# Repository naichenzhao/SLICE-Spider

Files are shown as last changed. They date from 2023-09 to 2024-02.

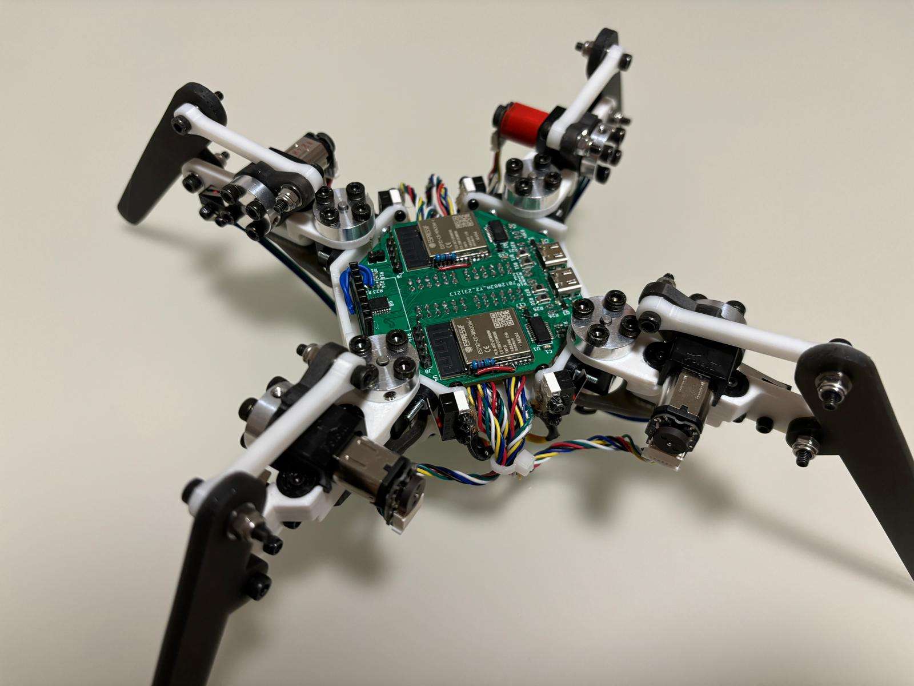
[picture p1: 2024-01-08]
images/IMG-20240107-WA0005.jpg

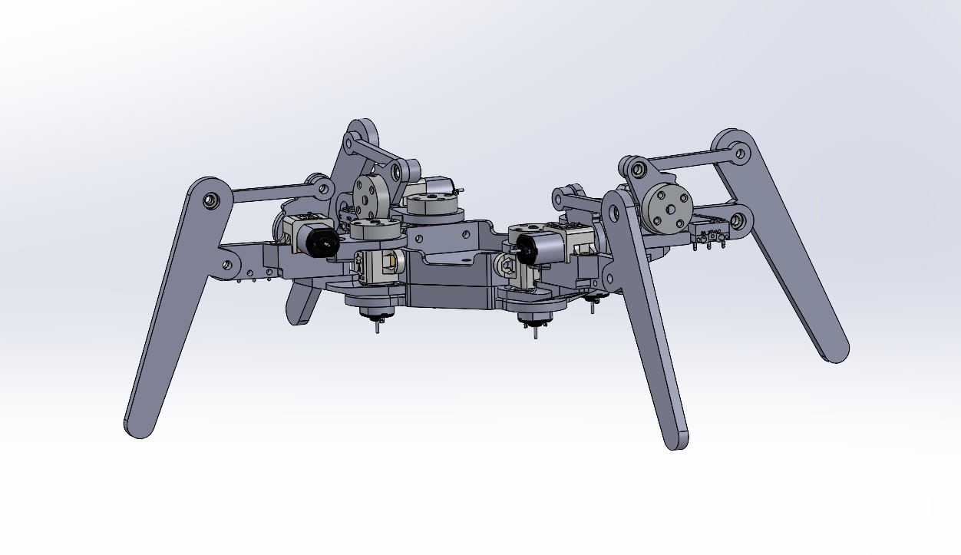
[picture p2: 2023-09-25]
images/Screenshot 2023-09-24 220727.jpg

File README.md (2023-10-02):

# Spider Bot for SLICE

something something, torque controlled robot spider



## Manufacturing
- SLS_Leg_Lower and SLS_Lever_Lower can be laser cut out of acrylic
- Everything else should be 3D printed

## BOM

Parts needed per spider
- 8x 12V DC Motor: https://www.pololu.com/product/3046
- 8x Enoder for motor: https://www.pololu.com/product/4761
- 8x M3 Motor hub w/ M3 screws: https://www.pololu.com/product/1996
- 8x Homing switches for the legs: https://www.amazon.com/Cylewet-25Pcs-Switch-Arduino-CYT1073/dp/B073TYWX86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
- 12x M3 flanged bearing for joints: https://www.amazon.com/uxcell-Flanged-3x6x2-5mm-Shielded-Bearings/dp/B08H27NJ5N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
- 16x M2 threaded heat insert: https://www.mcmaster.com/94180A307/

- Assortment of M2 and M3 screws/nuts

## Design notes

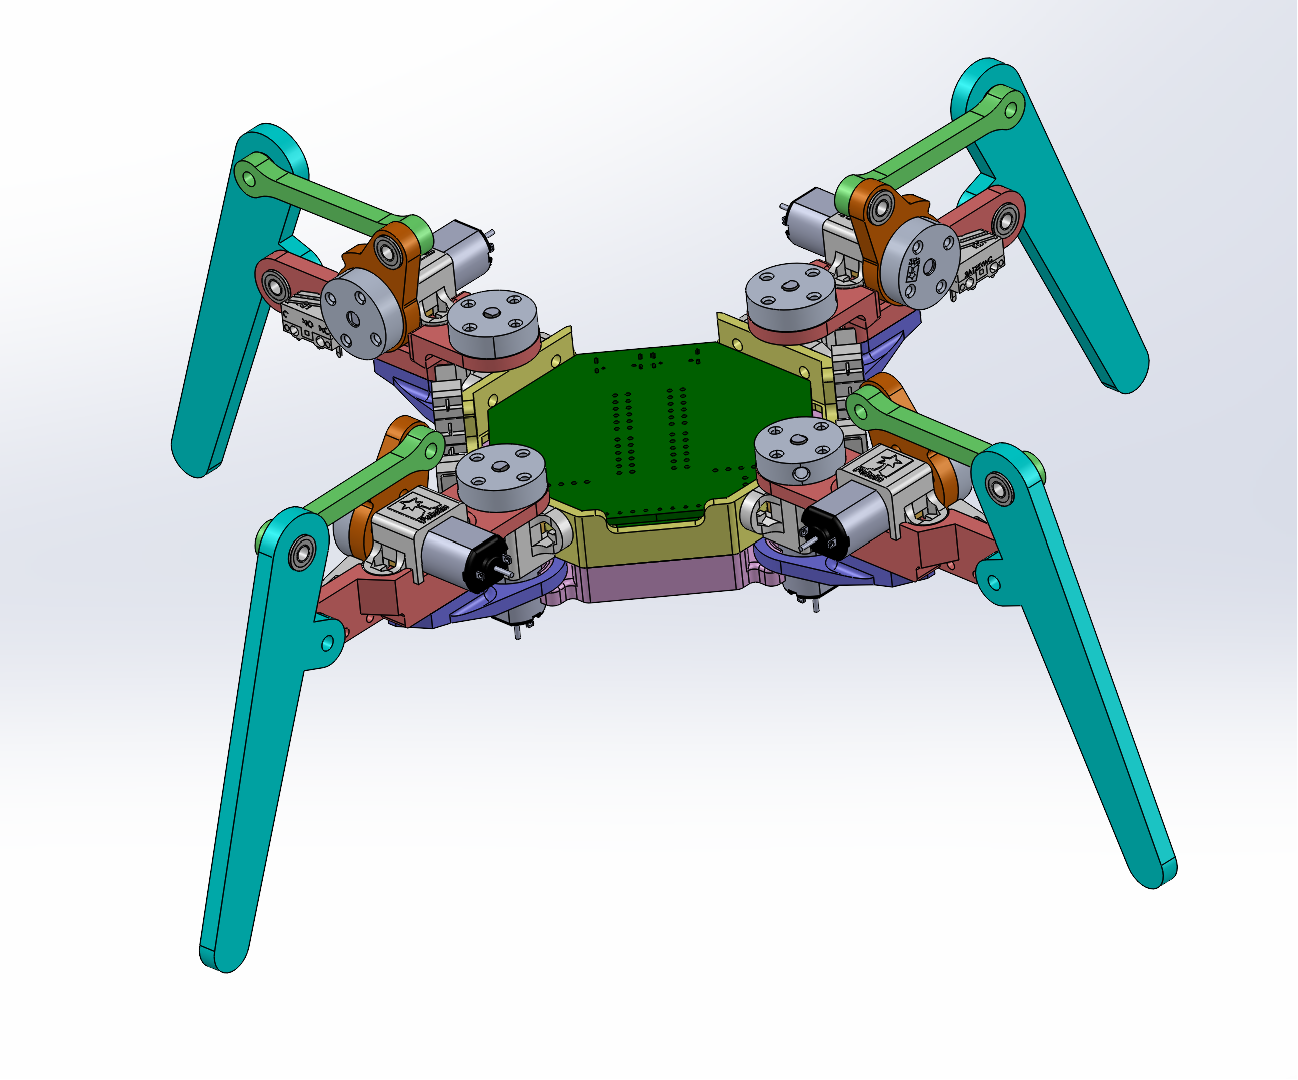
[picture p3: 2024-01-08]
images/Screenshot 2024-01-07 225647.png

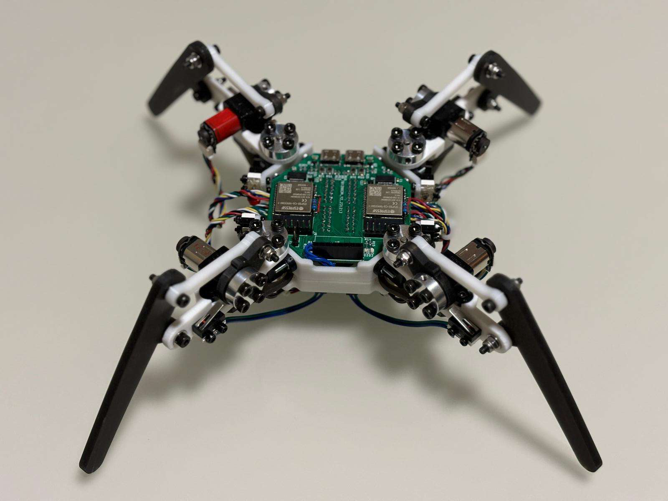
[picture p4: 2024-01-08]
images/IMG-20240107-WA0008.jpg

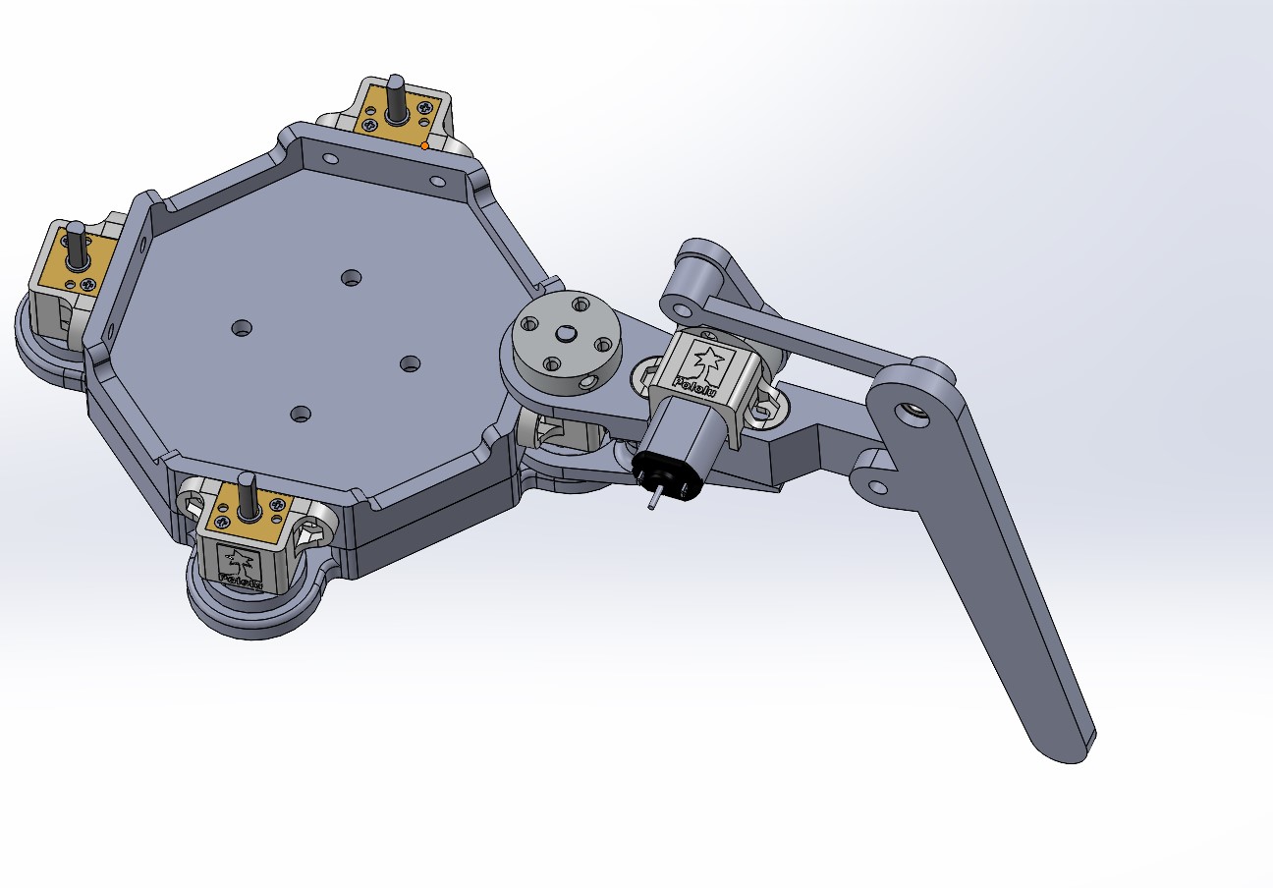
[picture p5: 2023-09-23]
images/Screenshot 2023-09-23 005408.jpg

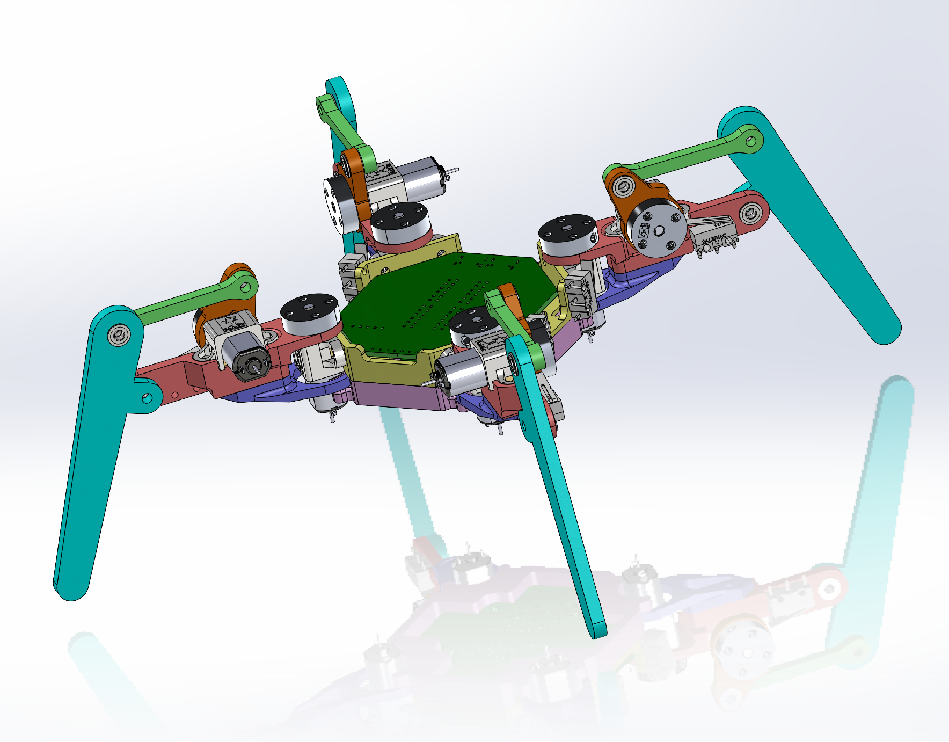
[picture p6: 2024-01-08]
images/Screenshot 2024-01-07 225526.png

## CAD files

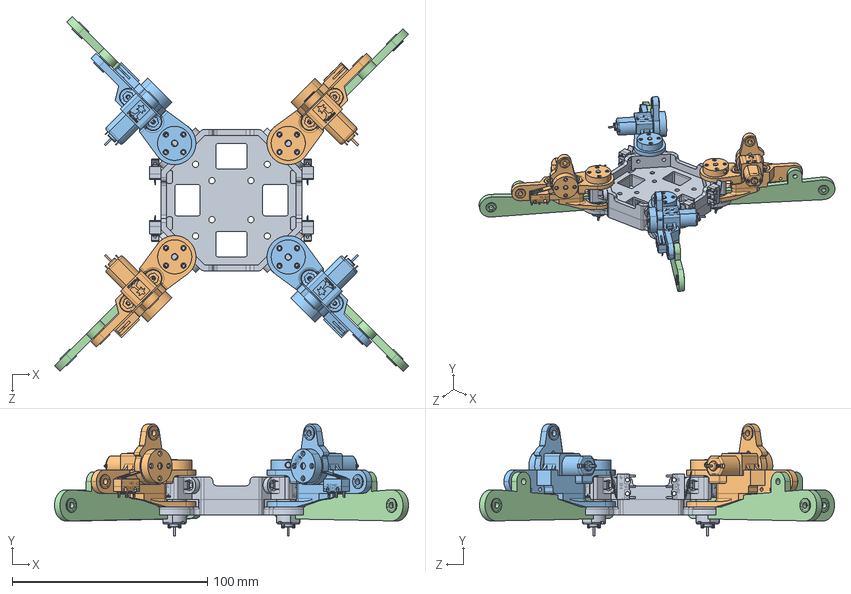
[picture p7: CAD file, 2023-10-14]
testing URDF Exporting/spider-viz.SLDASM
181.6 x 57.3 x 182.0 mm
Spider_body
Spider_upperleg_1 x 2
Spider_upperleg_2 x 2
Spider_lowerleg x 4

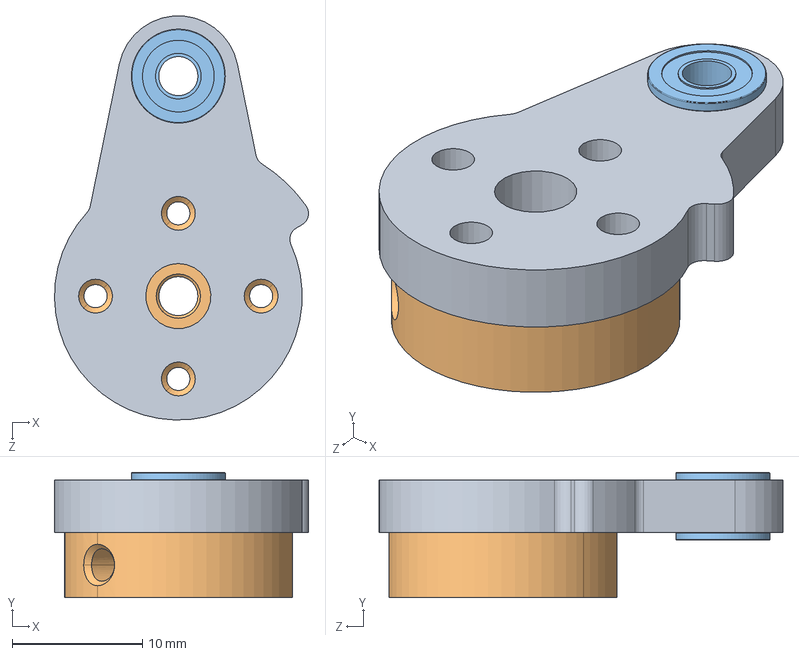
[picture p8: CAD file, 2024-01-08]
Solidoworks_Files/Spider_lever_2.SLDASM
19.5 x 9.60 x 31.0 mm
SLS_Lever_upper
shaft_mount
MF63zz 3x6x2.5mm Flanged Bearing.step x 2

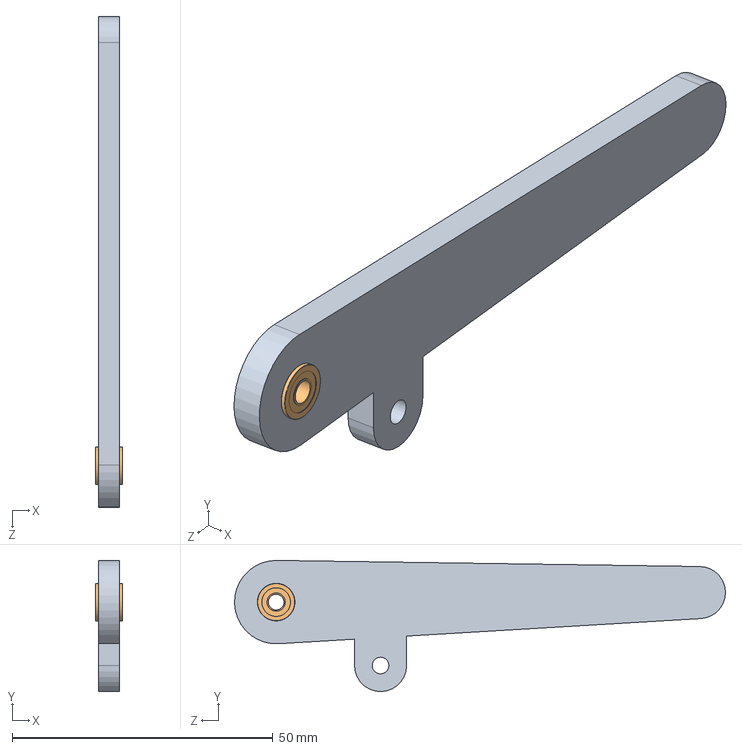
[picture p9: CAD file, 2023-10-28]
Solidoworks_Files/Spider_lowerleg.SLDASM
5.20 x 25.2 x 94.2 mm
SLS_leg_lower
MF63zz 3x6x2.5mm Flanged Bearing.step x 2

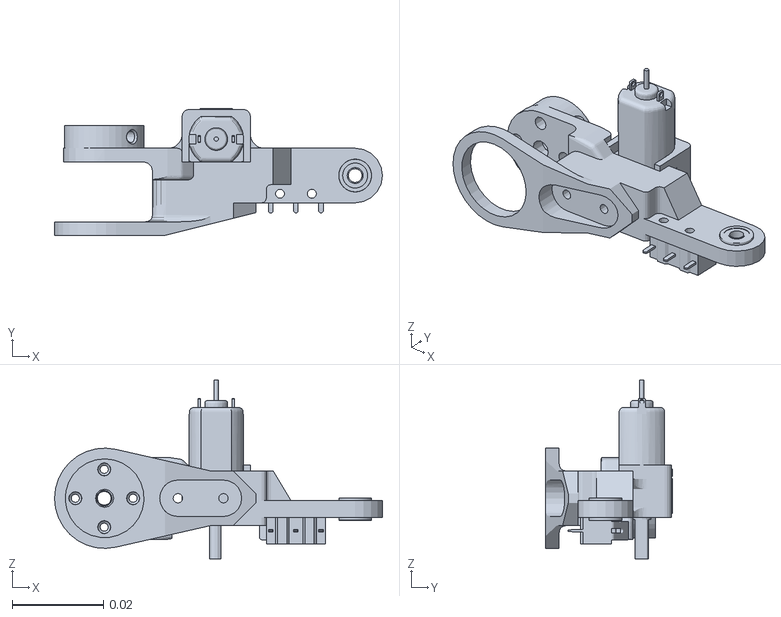
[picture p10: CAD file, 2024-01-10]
catkin_ws/src/spider-viz/meshes/Upper1_Link.STL
0.072 x 0.0279 x 0.0393

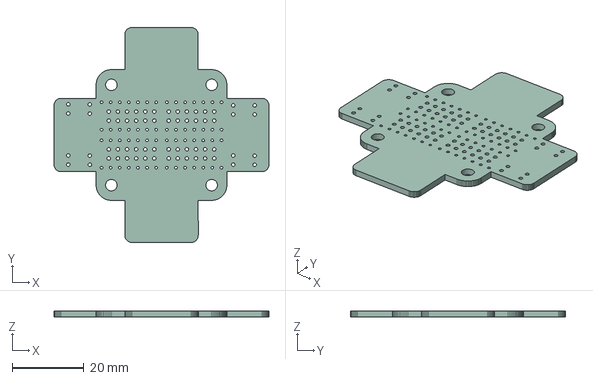
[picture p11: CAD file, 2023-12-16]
PCB/V1/Spider_Lower/Spider_Lower.step
60.0 x 60.0 x 1.58 mm

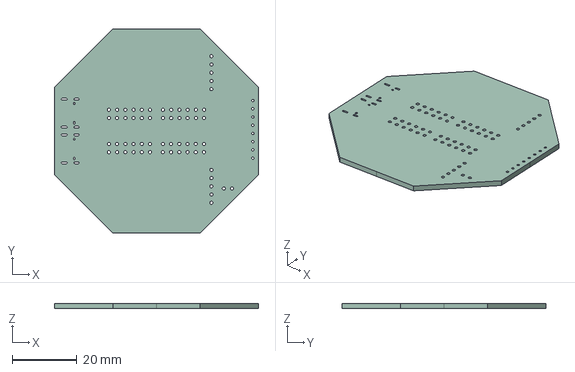
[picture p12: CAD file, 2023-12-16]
PCB/V1/Spider_Upper/Spider_Upper.step
63.0 x 63.0 x 1.58 mm

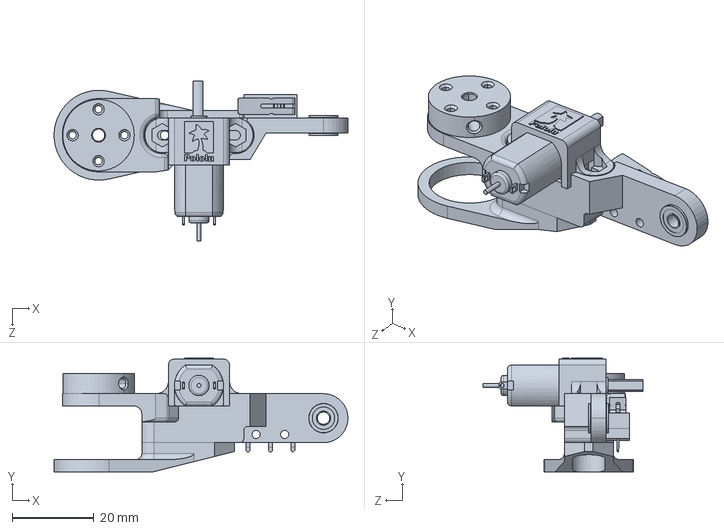
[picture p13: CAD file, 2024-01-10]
Solidoworks_Files/asm_parts/Spider_upperleg_1.SLDPRT
72.0 x 27.9 x 39.3 mm

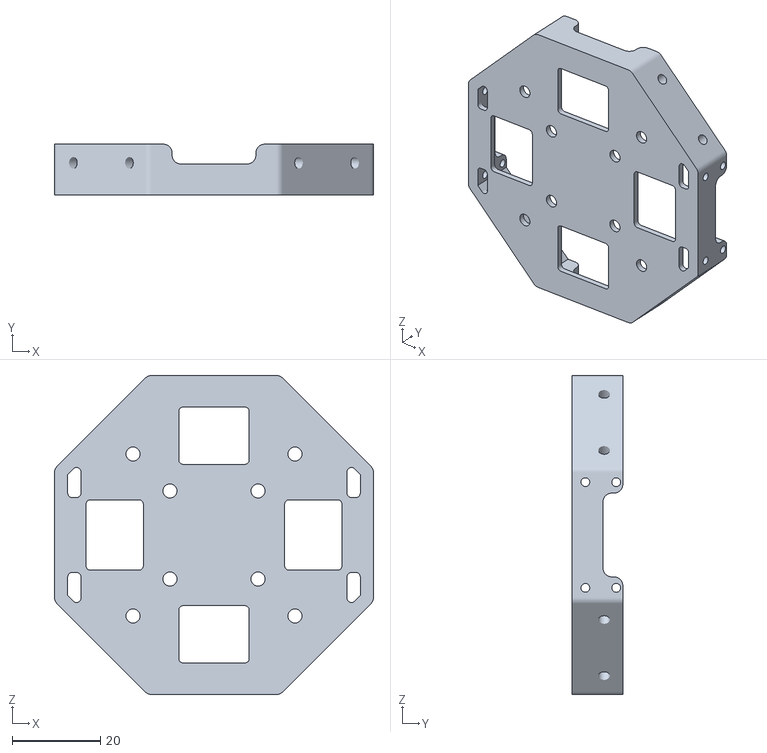
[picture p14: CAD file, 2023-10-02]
STL_Files/SLS_body.STL
72.4 x 11.5 x 72.4

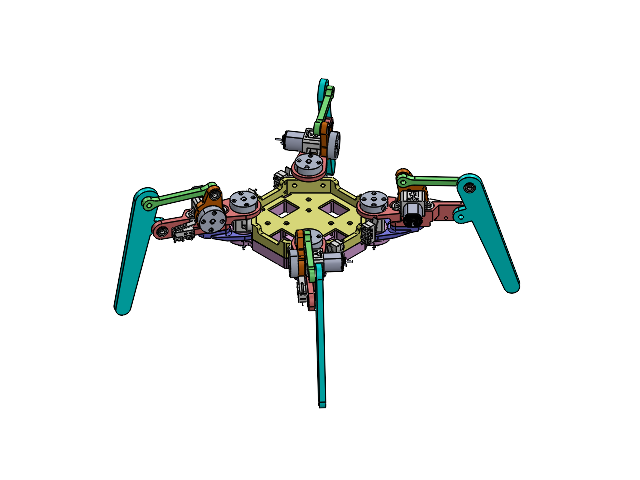
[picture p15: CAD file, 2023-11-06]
onshape_export/onshape_export.SLDASM
Spider_body
Spider_upperleg_1 x 2
Spider_upperleg_2 x 2
Spider_lowerleg x 4
SLS_lever_lower x 4
Spider_lever_2 x 2
Spider_lever x 2

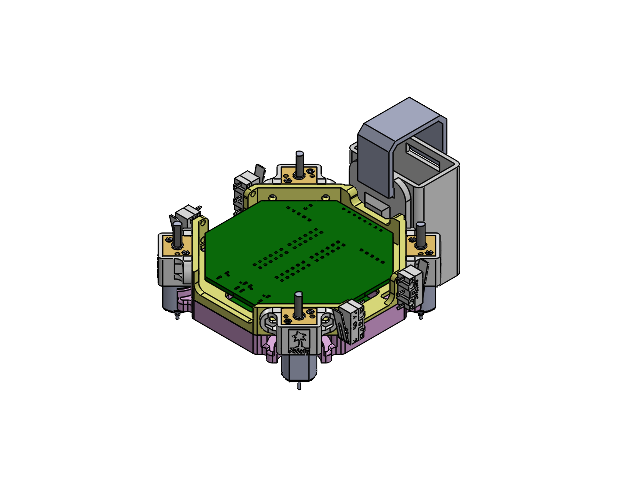
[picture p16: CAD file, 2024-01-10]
Solidoworks_Files/Spider_body.SLDASM
SLS_body
12V_Motor x 4
Limit_Switch x 4
SLS_lower_body
PCB_Lower
PCB_Upper
6mm_magnet x 4
batery_case
battery_case_clip

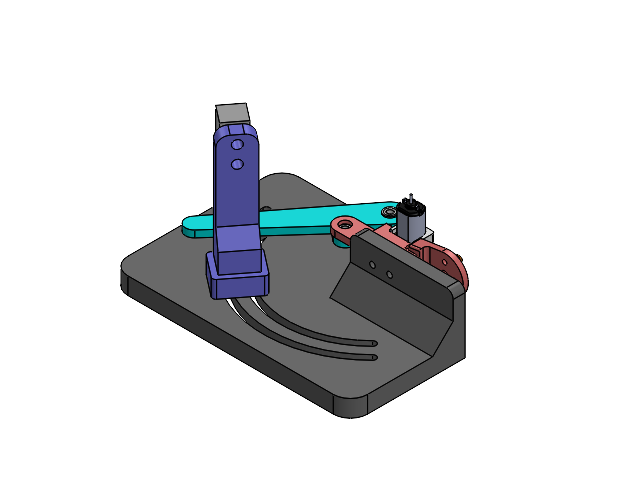
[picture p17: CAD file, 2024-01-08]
Testbenches/leg_TB_asm.SLDASM
leg_TB_frame
SLS_leg_upper_M
12V_Motor
MF63zz 3x6x2.5mm Flanged Bearing.step x 5
SLS_Lever_upper
shaft_mount
SLS_leg_lower
SLS_lever_lower
Strain_Gauge
Let_TB_slider

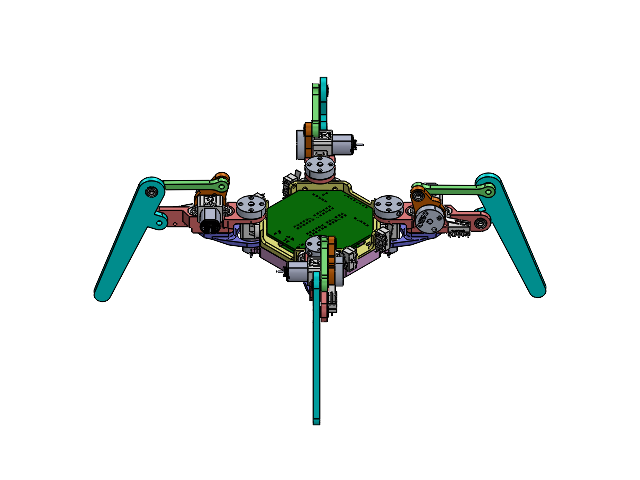
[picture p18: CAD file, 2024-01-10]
Solidoworks_Files/TLA_Spider.SLDASM
SLS_body
12V_Motor x 8
Limit_Switch x 8
SLS_lower_body
PCB_Lower
PCB_Upper
6mm_magnet x 4
batery_case
battery_case_clip
SLS_leg_upper x 2
MF63zz 3x6x2.5mm Flanged Bearing.step x 24
SLS_leg_upper_base x 4
shaft_mount x 8
SLS_leg_upper_M x 2
SLS_leg_lower x 4
SLS_lever_lower x 4
SLS_Lever_upper x 4

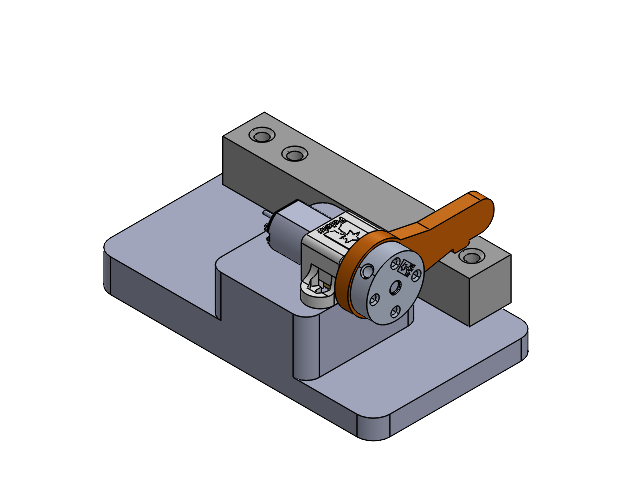
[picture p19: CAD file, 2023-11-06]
Testbenches/motor_TB_asm.SLDASM
motor_TB_frame
Strain_Gauge
12V_Motor
motor_TB_lever
shaft_mount

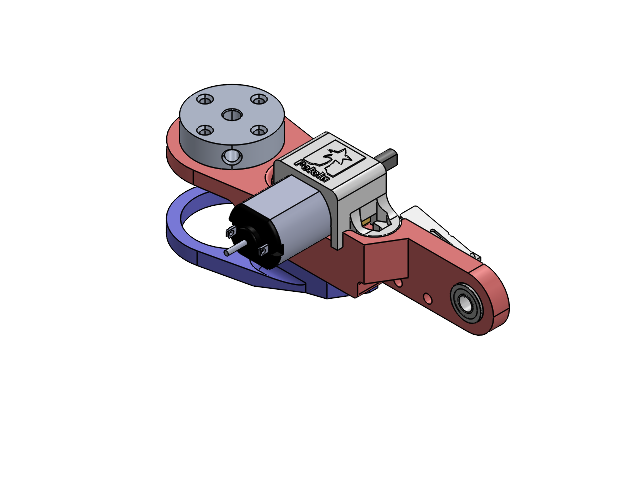
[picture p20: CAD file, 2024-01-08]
Solidoworks_Files/Spider_upperleg_1.SLDASM
SLS_leg_upper
Limit_Switch
12V_Motor
MF63zz 3x6x2.5mm Flanged Bearing.step x 2
SLS_leg_upper_base
shaft_mount

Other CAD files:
Solidoworks_Files/Spider_upperleg_2.SLDASM
Solidoworks_Files/Spider_lever.SLDASM
catkin_ws/src/spider-viz/meshes/Upper2_Link.STL
onshape_export/Spider_lever.SLDPRT
Archive/onshape_export/Spider_lever.SLDPRT
Archive/onshape_export/Spider_lever_2.SLDPRT
Archive/onshape_export/Spider_lowerleg.SLDPRT
Archive/onshape_export/Spider_upperleg_1.SLDPRT
Archive/onshape_export/Spider_upperleg_2.SLDPRT
Archive/testing URDF Exporting/Spider_lowerleg.SLDPRT
Archive/testing URDF Exporting/Spider_upperleg_1.SLDPRT
Archive/testing URDF Exporting/Spider_upperleg_2.SLDPRT
STL_Files/SLS_Lever_upper.STL
STL_Files/SLS_leg_lower.STL
STL_Files/SLS_leg_upper.STL
STL_Files/SLS_leg_upper_M.STL
STL_Files/SLS_leg_upper_base.STL
STL_Files/SLS_lever_lower.STL
STL_Files/SLS_lower_body.STL
Solidoworks_Files/12V_Motor.SLDPRT
Solidoworks_Files/6mm_magnet.SLDPRT
Solidoworks_Files/Limit_Switch.SLDPRT
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

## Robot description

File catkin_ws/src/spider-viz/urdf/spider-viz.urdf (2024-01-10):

<?xml version="1.0" encoding="utf-8"?>
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
<robot name="spider-viz">
  <link name="base_link">
    <inertial>
      <origin xyz="0.0266900629514275 0.0373682215528626 0.0414401671660664" rpy="0 0 0" />
      <mass value="0.0599747186219502" />
      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
    </inertial>
    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
  </link>
  <link name="Upper0_Link">
    <inertial>
      <origin xyz="0.021476139074384 0.015254727578512 -0.0014907670536348" rpy="0 0 0" />
      <mass value="0.0112993413960727" />
      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
    </inertial>
    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
  </link>
  <joint name="Upper0" type="revolute">
    <origin xyz="-0.00245284745286685 -0.0237725392912402 0.0320074126580795" rpy="1.5707963267949 0 3.14159265358979" />
    <parent link="base_link" />
    <child link="Upper0_Link" />
    <axis xyz="0 1 0" />
    <limit effort="1000.0" lower="-1.57" upper="0.17" velocity="0.5"/>
  </joint>
  <link name="Lower0_Link">
    <inertial>
      <origin xyz="-0.00200000000000073 -0.0121644422551732 0.0152866791815001" rpy="0 0 0" />
      <mass value="0.00511403475106287" />
      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
    </inertial>
    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
  </link>
  <joint name="Lower0" type="revolute">
    <origin xyz="0.0550943670538193 0.01315 -9.9999999999479E-05" rpy="1.57079632679491 -1.5707963267949 0" />
    <parent link="Upper0_Link" />
    <child link="Lower0_Link" />
    <axis xyz="1 0 0" />
    <limit effort="1000.0" lower="-0.96" upper="0.70" velocity="0.5"/>
  </joint>
  <link name="Upper1_Link">
    <inertial>
      <origin xyz="0.0213801728228362 0.0152547283369141 0.0014673545578197" rpy="0 0 0" />
      <mass value="0.0112993383446934" />
      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
    </inertial>
    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
  </link>
  <joint name="Upper1" type="revolute">
    <origin xyz="-0.0024528474528662 -0.0820568105387026 0.0320074126580794" rpy="1.5707963267949 0 3.14159265358979" />
    <parent link="base_link" />
    <child link="Upper1_Link" />
    <axis xyz="0 1 0" />
      <limit effort="1000.0" lower="-0.17" upper="1.85" velocity="0.5"/>
  </joint>
  <link name="Lower1_Link">
    <inertial>
      <origin xyz="0.0020000000000001 -0.012164442255174 0.0152866791815" rpy="0 0 0" />
      <mass value="0.00511403475106288" />
      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
    </inertial>
    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
  </link>
  <joint name="Lower1" type="revolute">
    <origin xyz="0.055 0.0131500000000001 9.99999999997392E-05" rpy="1.57079632679491 -1.5707963267949 0" />
    <parent link="Upper1_Link" />
    <child link="Lower1_Link" />
    <axis xyz="1 0 0" />
    <limit effort="1000.0" lower="-0.96" upper="0.70" velocity="0.5"/>
  </joint>
  <link name="Upper2_Link">
    <inertial>
      <origin xyz="0.0214745398766555 0.0152547283369141 0.00146735455781985" rpy="0 0 0" />
      <mass value="0.0112993383446934" />
      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
    </inertial>
    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
  </link>
  <joint name="Upper2" type="revolute">
    <origin xyz="0.055831423794595 -0.02377253929124 0.0320074126580794" rpy="1.5707963267949 0 0" />
    <parent link="base_link" />
    <child link="Upper2_Link" />
    <axis xyz="0 1 0" />
    <limit effort="1000.0" lower="-0.17" upper="1.57" velocity="0.5"/>
  </joint>
  <link name="Lower2_Link">
    <inertial>
      <origin xyz="0.00200000000000116 -0.0121644422551723 0.0152866791815003" rpy="0 0 0" />
      <mass value="0.00511403475106288" />
      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
    </inertial>
    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
  </link>
  <joint name="Lower2" type="revolute">
    <origin xyz="0.0550943670538194 0.0131500000000001 0.000100000000000329" rpy="1.57079632679489 -1.5707963267949 0" />
    <parent link="Upper2_Link" />
    <child link="Lower2_Link" />
    <axis xyz="1 0 0" />
    <limit effort="1000.0" lower="-0.96" upper="0.70" velocity="0.5"/>
  </joint>
  <link name="Upper3_Link">
    <inertial>
      <origin xyz="0.0214761390743841 0.0152547275785121 -0.00149076705363482" rpy="0 0 0" />
      <mass value="0.0112993413960727" />
      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
    </inertial>
    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
  </link>
  <joint name="Upper3" type="revolute">
    <origin xyz="0.0558314237945942 -0.082056810538703 0.0320074126580794" rpy="1.5707963267949 0 0" />
    <parent link="base_link" />
    <child link="Upper3_Link" />
    <axis xyz="0 1 0" />
    <limit effort="1000.0" lower="-1.85" upper="0.17" velocity="0.5"/>
  </joint>
  <link name="Lower3_Link">
    <inertial>
      <origin xyz="-0.00200000000000015 -0.0121644422551734 0.0152866791814997" rpy="0 0 0" />
      <mass value="0.00511403475106288" />
      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
    </inertial>
    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
  </link>
  <joint name="Lower3" type="revolute">
    <origin xyz="0.0550943670538194 0.0131500000000001 -0.000100000000001266" rpy="1.57079632679489 -1.5707963267949 0" />
    <parent link="Upper3_Link" />
    <child link="Lower3_Link" />
    <axis xyz="1 0 0" />
    <limit effort="1000.0" lower="-0.96" upper="0.70" velocity="0.5"/>
  </joint>
</robot>

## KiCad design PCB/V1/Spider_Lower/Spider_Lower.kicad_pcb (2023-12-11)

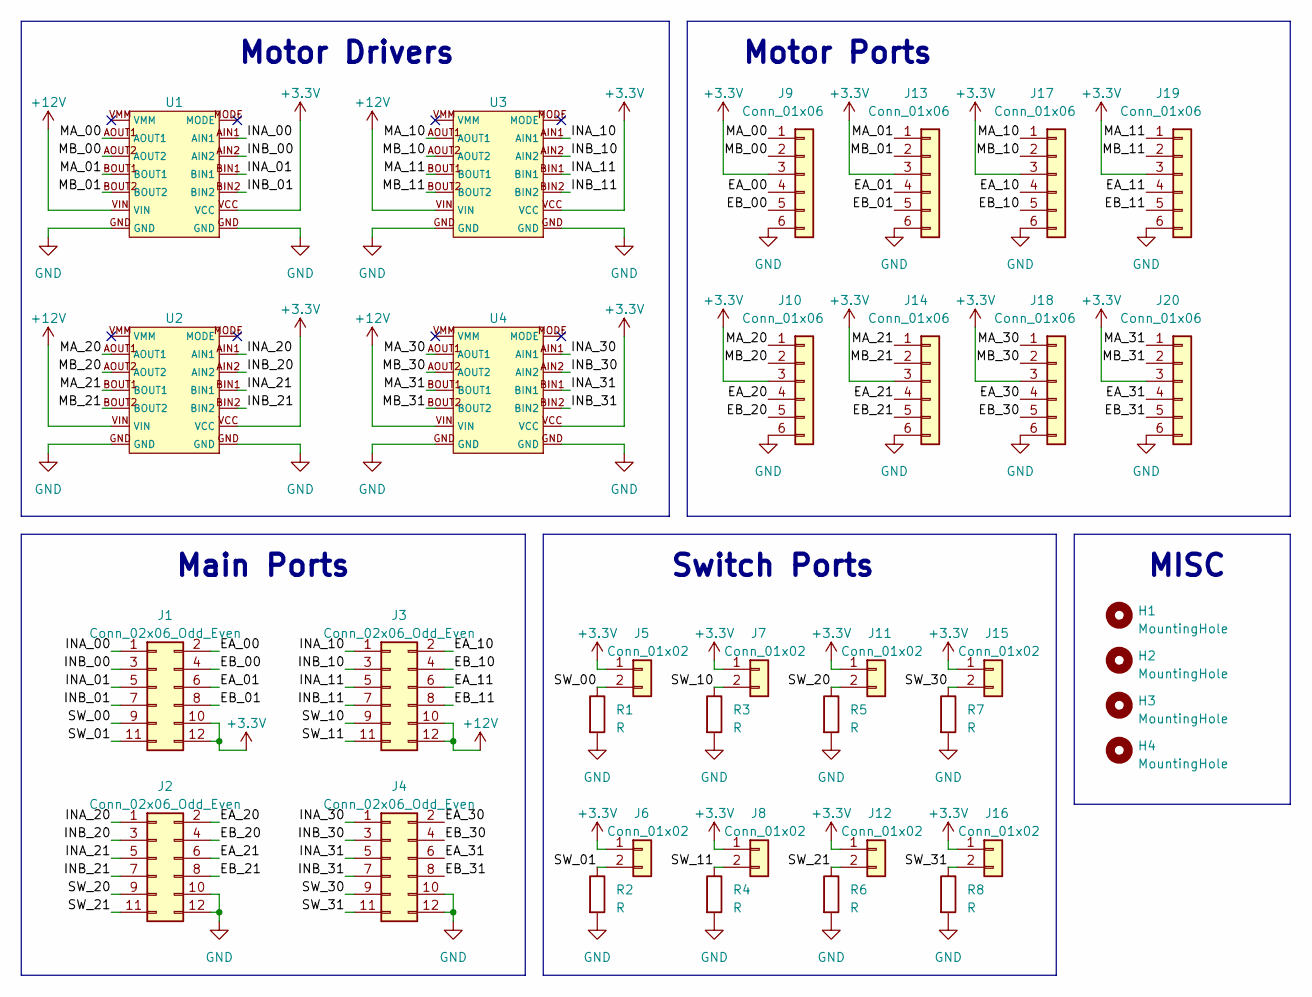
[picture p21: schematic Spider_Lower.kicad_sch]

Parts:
H1, H2, H3, H4: MountingHole; MountingHole_3.2mm_M3
J1, J2, J3, J4: Conn_02x06_Odd_Even; PinHeader_2x06_P2.54mm_Vertical
J5, J6, J7, J8, J11, J12, J15, J16: Conn_01x02; PinHeader_1x02_P2.54mm_Vertical
J9, J10, J13, J14, J17, J18, J19, J20: Conn_01x06; JST_SH_BM06B-SRSS-TB_1x06-1MP_P1.00mm_Vertical
R1, R2, R4, R5, R6, R7, R8: R; R_0805_2012Metric
R3: R; C_0805_2012Metric
U1, U2, U3, U4: DRV8835

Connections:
+3.3V: J1.10, J1.12, J5.1, J6.1, J7.1, J8.1, J9.3, J10.3, J11.1, J12.1, J13.3, J14.3, J15.1, J16.1, J17.3, J18.3, J19.3, J20.3, U1.VCC, U2.VCC, U3.VCC, U4.VCC
+12V: J3.10, J3.12, U1.VIN, U2.VIN, U3.VIN, U4.VIN
/EA_00: J1.2, J9.4
/EA_01: J1.6, J13.4
/EA_10: J3.2, J17.4
/EA_11: J3.6, J19.4
/EA_20: J2.2, J10.4
/EA_21: J2.6, J14.4
/EA_30: J4.2, J18.4
/EA_31: J4.6, J20.4
/EB_00: J1.4, J9.5
/EB_01: J1.8, J13.5
/EB_10: J3.4, J17.5
/EB_11: J3.8, J19.5
/EB_20: J2.4, J10.5
/EB_21: J2.8, J14.5
/EB_30: J4.4, J18.5
/EB_31: J4.8, J20.5
/INA_00: J1.1, U1.AIN1
/INA_01: J1.5, U1.BIN1
/INA_10: J3.1, U3.AIN1
/INA_11: J3.5, U3.BIN1
/INA_20: J2.1, U2.AIN1
/INA_21: J2.5, U2.BIN1
/INA_30: J4.1, U4.AIN1
/INA_31: J4.5, U4.BIN1
/INB_00: J1.3, U1.AIN2
/INB_01: J1.7, U1.BIN2
/INB_10: J3.3, U3.AIN2
/INB_11: J3.7, U3.BIN2
/INB_20: J2.3, U2.AIN2
/INB_21: J2.7, U2.BIN2
/INB_30: J4.3, U4.AIN2
/INB_31: J4.7, U4.BIN2
/MA_00: J9.1, U1.AOUT1
/MA_01: J13.1, U1.BOUT1
/MA_10: J17.1, U3.AOUT1
/MA_11: J19.1, U3.BOUT1
/MA_20: J10.1, U2.AOUT1
/MA_21: J14.1, U2.BOUT1
/MA_30: J18.1, U4.AOUT1
/MA_31: J20.1, U4.BOUT1
/MB_00: J9.2, U1.AOUT2
/MB_01: J13.2, U1.BOUT2
/MB_10: J17.2, U3.AOUT2
/MB_11: J19.2, U3.BOUT2
/MB_20: J10.2, U2.AOUT2
/MB_21: J14.2, U2.BOUT2
/MB_30: J18.2, U4.AOUT2
/MB_31: J20.2, U4.BOUT2
/SW_00: J1.9, J5.2, R1.1
/SW_01: J1.11, J6.2, R2.1
/SW_10: J3.9, J7.2, R3.1
/SW_11: J3.11, J8.2, R4.1
/SW_20: J2.9, J11.2, R5.1
/SW_21: J2.11, J12.2, R6.1
/SW_30: J4.9, J15.2, R7.1
/SW_31: J4.11, J16.2, R8.1
GND: J2.10, J2.12, J4.10, J4.12, J9.6, J10.6, J13.6, J14.6, J17.6, J18.6, J19.6, J20.6, R1.2, R2.2, R3.2, R4.2, R5.2, R6.2, R7.2, R8.2, U1.GND, U2.GND, U3.GND, U4.GND

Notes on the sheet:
Main Ports
Motor Ports
Motor Drivers
Switch Ports
MISC

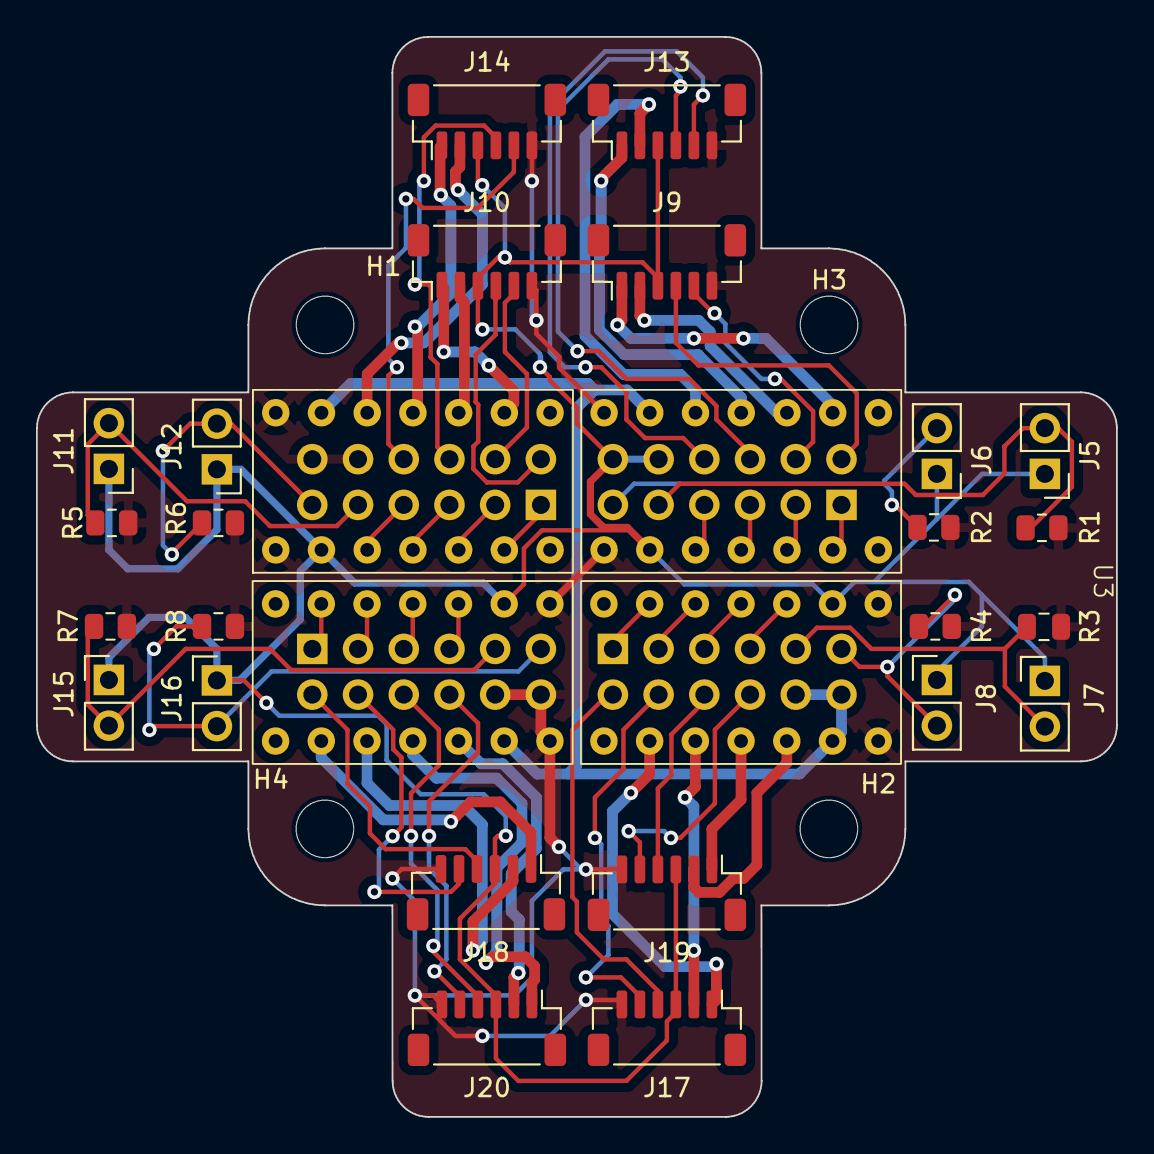
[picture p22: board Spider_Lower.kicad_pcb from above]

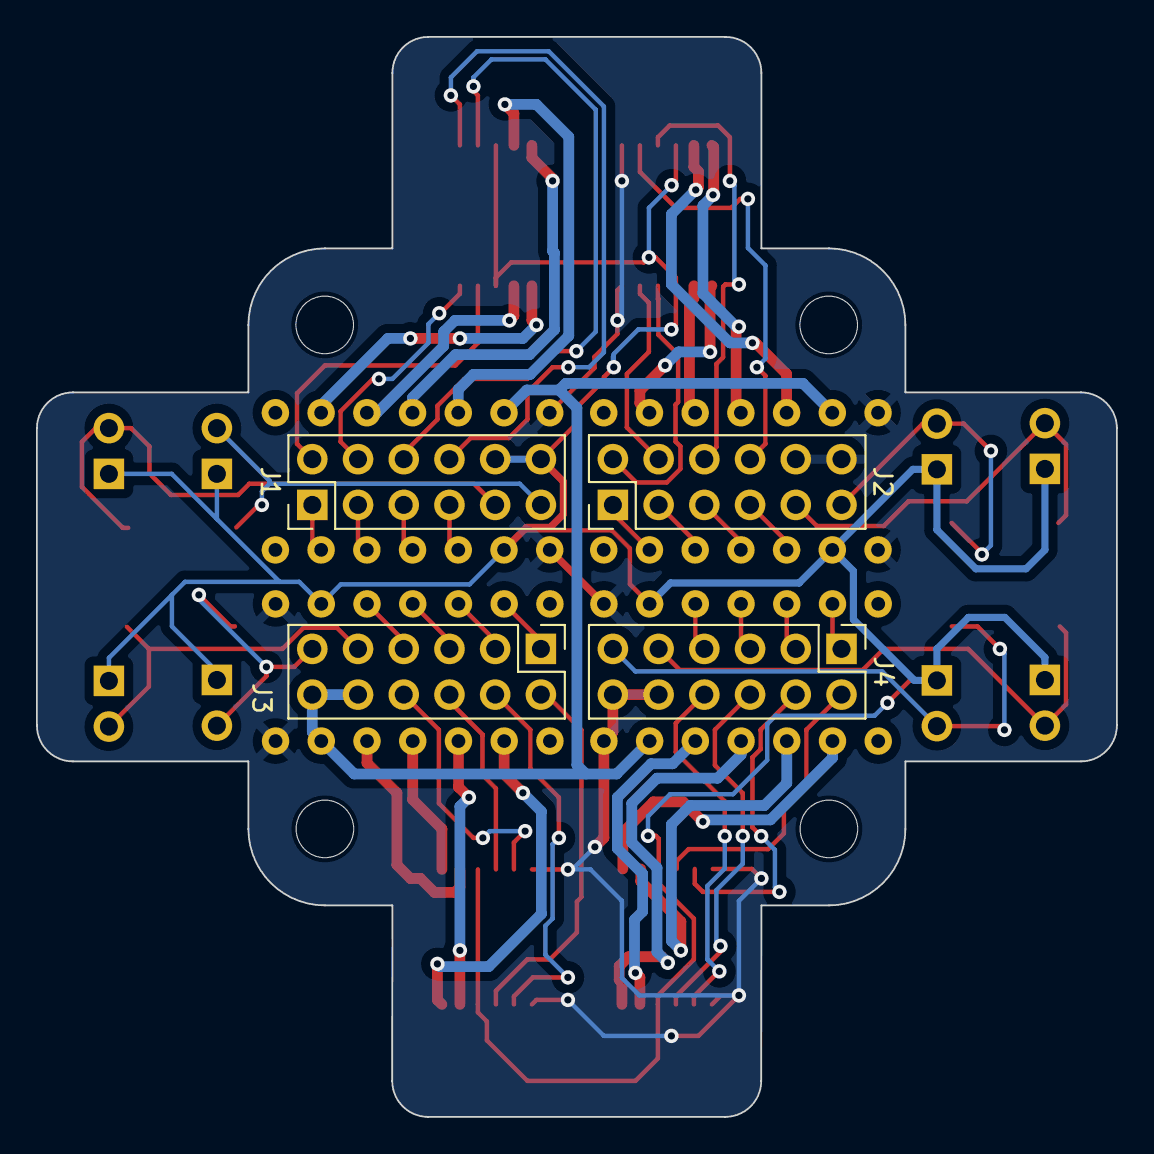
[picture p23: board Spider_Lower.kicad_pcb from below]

Board: 2 copper layers, 60.0 x 60.0 mm, 36 parts (4 on the bottom side), 59 nets.

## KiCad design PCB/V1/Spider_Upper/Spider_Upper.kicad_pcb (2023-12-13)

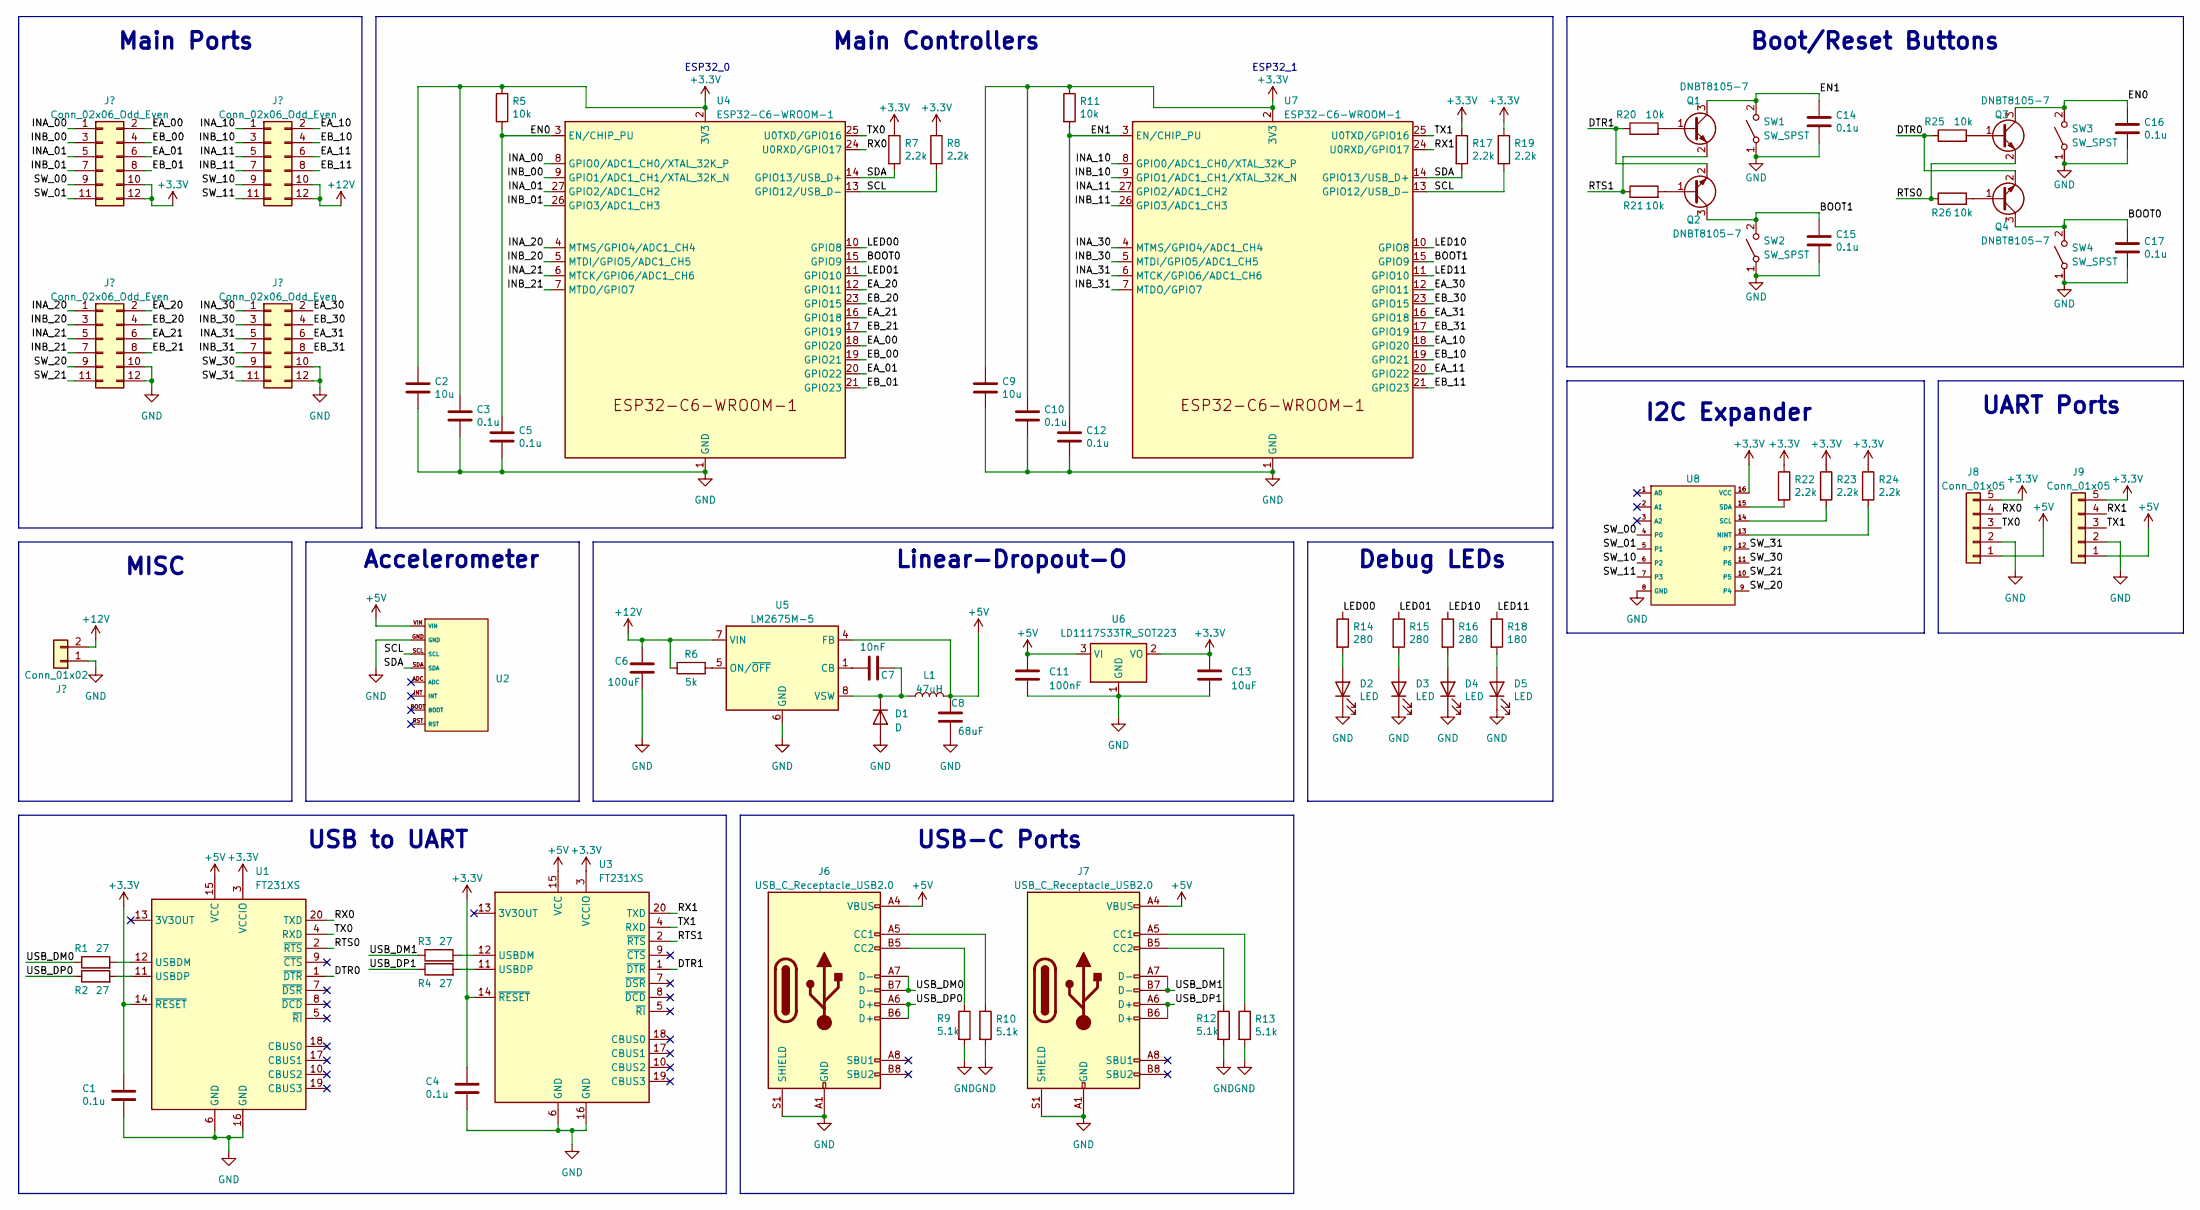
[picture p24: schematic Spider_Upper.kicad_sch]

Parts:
C1, C3, C4, C5, C10, C12, C14, C15, C16, C17: 0.1u; C_0603_1608Metric_Pad1.08x0.95mm_HandSolder
C2, C9: 10u; C_0603_1608Metric_Pad1.08x0.95mm_HandSolder
C6: 100uF; C_0805_2012Metric
C7: 10nF; C_0805_2012Metric
C8: 68uF; C_0805_2012Metric
C11: 100nF; C_0805_2012Metric
C13: 10uF; C_0805_2012Metric
D1: D; D_0805_2012Metric
D2, D3, D4, D5: LED; LED_0805_2012Metric_Pad1.15x1.40mm_HandSolder
J1, J2, J3, J4: Conn_02x06_Odd_Even; PinHeader_2x06_P2.54mm_Vertical
J5: Conn_01x02; PinHeader_1x02_P2.54mm_Vertical
J6, J7: USB_C_Receptacle_USB2.0; USB_C_Receptacle_JAE_DX07S016JA1R1500
J8, J9: Conn_01x05; PinHeader_1x05_P2.54mm_Vertical
L1: 47uH; L_0805_2012Metric
Q1, Q2, Q3, Q4: DNBT8105-7; SOT-23
R1, R2, R3, R4: 27; R_0603_1608Metric_Pad0.98x0.95mm_HandSolder
R5, R11, R20, R21, R25, R26: 10k; R_0603_1608Metric_Pad0.98x0.95mm_HandSolder
R6: 5k; R_0805_2012Metric
R7, R8, R17, R19, R22, R23, R24: 2.2k; R_0603_1608Metric_Pad0.98x0.95mm_HandSolder
R9, R10, R12, R13: 5.1k; R_0603_1608Metric_Pad0.98x0.95mm_HandSolder
R14, R15, R16: 280; R_0603_1608Metric_Pad0.98x0.95mm_HandSolder
R18: 180; R_0603_1608Metric_Pad0.98x0.95mm_HandSolder
SW1, SW2, SW3, SW4: SW_SPST; SW_SPST_B3U-1000P
U1, U3: FT231XS; SSOP-20_3.9x8.7mm_P0.635mm
U2: BNO055
U4, U7: ESP32-C6-WROOM-1
U5: LM2675M-5; SOIC-8_3.9x4.9mm_P1.27mm
U6: LD1117S33TR_SOT223; SOT-223-3_TabPin2
U8: TSSOP-16-1EP_4.4x5mm_P0.65mm

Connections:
+3.3V: C1.1, C2.1, C3.1, C4.1, C9.1, C10.1, C13.1, J1.10, J1.12, J8.5, J9.5, R5.1, R7.1, R8.1, R11.1, R17.1, R19.1, R22.1, R23.1, R24.1, U1.3 (VCCIO), U1.14 (~RESET), U3.3 (VCCIO), U3.14 (~RESET), U4.2 (3V3), U6.2 (VO), U7.2 (3V3), U8.16 (VCC)
+5V: C8.1, C11.1, J6.A4 (VBUS), J6.A9 (VBUS), J6.B4 (VBUS), J6.B9 (VBUS), J7.A4 (VBUS), J7.A9 (VBUS), J7.B4 (VBUS), J7.B9 (VBUS), J8.1, J9.1, L1.2, U1.15 (VCC), U2.VIN, U3.15 (VCC), U5.4 (FB), U6.3 (VI)
+12V: C6.1, J3.10, J3.12, J5.2, R6.1, U5.7 (VIN)
/BOOT0: C17.1, Q4.3 (C), SW4.2 (B), U4.15 (GPIO9)
/BOOT1: C15.1, Q2.3 (C), SW2.2 (B), U7.15 (GPIO9)
/DTR0: Q4.2 (E), R25.1, U1.1 (~DTR)
/DTR1: Q2.2 (E), R20.1, U3.1 (~DTR)
/EA_00: J1.2, U4.18 (GPIO20)
/EA_01: J1.6, U4.20 (GPIO22)
/EA_10: J3.2, U7.18 (GPIO20)
/EA_11: J3.6, U7.20 (GPIO22)
/EA_20: J2.2, U4.12 (GPIO11)
/EA_21: J2.6, U4.16 (GPIO18)
/EA_30: J4.2, U7.12 (GPIO11)
/EA_31: J4.6, U7.16 (GPIO18)
/EB_00: J1.4, U4.19 (GPIO21)
/EB_01: J1.8, U4.21 (GPIO23)
/EB_10: J3.4, U7.19 (GPIO21)
/EB_11: J3.8, U7.21 (GPIO23)
/EB_20: J2.4, U4.23 (GPIO15)
/EB_21: J2.8, U4.17 (GPIO19)
/EB_30: J4.4, U7.23 (GPIO15)
/EB_31: J4.8, U7.17 (GPIO19)
/EN0: C5.1, C16.1, Q3.3 (C), R5.2, SW3.2 (B), U4.3 (EN/CHIP_PU)
/EN1: C12.1, C14.1, Q1.3 (C), R11.2, SW1.2 (B), U7.3 (EN/CHIP_PU)
/INA_00: J1.1, U4.8 (GPIO0/ADC1_CH0/XTAL_32K_P)
/INA_01: J1.5, U4.27 (GPIO2/ADC1_CH2)
/INA_10: J3.1, U7.8 (GPIO0/ADC1_CH0/XTAL_32K_P)
/INA_11: J3.5, U7.27 (GPIO2/ADC1_CH2)
/INA_20: J2.1, U4.4 (MTMS/GPIO4/ADC1_CH4)
/INA_21: J2.5, U4.6 (MTCK/GPIO6/ADC1_CH6)
/INA_30: J4.1, U7.4 (MTMS/GPIO4/ADC1_CH4)
/INA_31: J4.5, U7.6 (MTCK/GPIO6/ADC1_CH6)
/INB_00: J1.3, U4.9 (GPIO1/ADC1_CH1/XTAL_32K_N)
/INB_01: J1.7, U4.26 (GPIO3/ADC1_CH3)
/INB_10: J3.3, U7.9 (GPIO1/ADC1_CH1/XTAL_32K_N)
/INB_11: J3.7, U7.26 (GPIO3/ADC1_CH3)
/INB_20: J2.3, U4.5 (MTDI/GPIO5/ADC1_CH5)
/INB_21: J2.7, U4.7 (MTDO/GPIO7)
/INB_30: J4.3, U7.5 (MTDI/GPIO5/ADC1_CH5)
/INB_31: J4.7, U7.7 (MTDO/GPIO7)
/LED00: R14.1, U4.10 (GPIO8)
/LED01: R15.1, U4.11 (GPIO10)
/LED10: R16.1, U7.10 (GPIO8)
/LED11: R18.1, U7.11 (GPIO10)
/RTS0: Q3.2 (E), R26.1, U1.2 (~RTS)
/RTS1: Q1.2 (E), R21.1, U3.2 (~RTS)
/RX0: J8.4, U1.20 (TXD), U4.24 (U0RXD/GPIO17)
/RX1: J9.4, U3.20 (TXD), U7.24 (U0RXD/GPIO17)
/SCL: R8.2, R19.2, U2.SCL, U4.13 (GPIO12/USB_D-), U7.13 (GPIO12/USB_D-)
/SDA: R7.2, R17.2, U2.SDA, U4.14 (GPIO13/USB_D+), U7.14 (GPIO13/USB_D+)
/SW_00: J1.9, U8.4 (P0)
/SW_01: J1.11, U8.5 (P1)
/SW_10: J3.9, U8.6 (P2)
/SW_11: J3.11, U8.7 (P3)
/SW_20: J2.9, U8.9 (P4)
/SW_21: J2.11, U8.10 (P5)
/SW_30: J4.9, U8.11 (P6)
/SW_31: J4.11, U8.12 (P7)
/TX0: J8.3, U1.4 (RXD), U4.25 (U0TXD/GPIO16)
/TX1: J9.3, U3.4 (RXD), U7.25 (U0TXD/GPIO16)
/USB_DM0: J6.A7 (D-), J6.B7 (D-), R1.1
/USB_DM1: J7.A7 (D-), J7.B7 (D-), R3.1
/USB_DP0: J6.A6 (D+), J6.B6 (D+), R2.1
/USB_DP1: J7.A6 (D+), J7.B6 (D+), R4.1
GND: C1.2, C2.2, C3.2, C4.2, C5.2, C6.2, C8.2, C9.2, C10.2, C11.2, C12.2, C13.2, C14.2, C15.2, C16.2, C17.2, D1.2 (A), D2.1 (K), D3.1 (K), D4.1 (K), D5.1 (K), J2.10, J2.12, J4.10, J4.12, J5.1, J6.A1 (GND), J6.A12 (GND), J6.B1 (GND), J6.B12 (GND), J6.S1 (SHIELD), J7.A1 (GND), J7.A12 (GND), J7.B1 (GND), J7.B12 (GND), J7.S1 (SHIELD), J8.2, J9.2, R9.2, R10.2, R12.2, R13.2, SW1.1 (A), SW2.1 (A), SW3.1 (A), SW4.1 (A), U1.6 (GND), U1.16 (GND), U2.GND, U3.6 (GND), U3.16 (GND), U4.1 (GND), U4.28 (GND), U4.29 (GND), U5.6 (GND), U6.1 (GND), U7.1 (GND), U7.28 (GND), U7.29 (GND), U8.8 (GND)
unnamed: C7.1, D1.1 (K), L1.1, U5.8 (VSW)
unnamed: D2.2 (A), R14.2
unnamed: D3.2 (A), R15.2
unnamed: D4.2 (A), R16.2
unnamed: D5.2 (A), R18.2
unnamed: J6.A5 (CC1), R10.1
unnamed: J6.B5 (CC2), R9.1
unnamed: J7.A5 (CC1), R13.1
unnamed: J7.B5 (CC2), R12.1
unnamed: Q1.1 (B), R20.2
unnamed: Q2.1 (B), R21.2
unnamed: Q3.1 (B), R25.2
unnamed: Q4.1 (B), R26.2
unnamed: R1.2, U1.12 (USBDM)
unnamed: R2.2, U1.11 (USBDP)
unnamed: R3.2, U3.12 (USBDM)
unnamed: R4.2, U3.11 (USBDP)
unnamed: C7.2, U5.1 (CB)
unnamed: R6.2, U5.5 (ON/~OFF)
unnamed: R24.2, U8.13 (NINT)
unnamed: R23.2, U8.14 (SCL)
unnamed: R22.2, U8.15 (SDA)

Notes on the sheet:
Debug LEDs
Linear-Dropout-O
USB to UART
MISC
Main Controllers
UART Ports
I2C Expander
USB-C Ports
Accelerometer
Boot/Reset Buttons
ESP32_0
ESP32_1
Main Ports

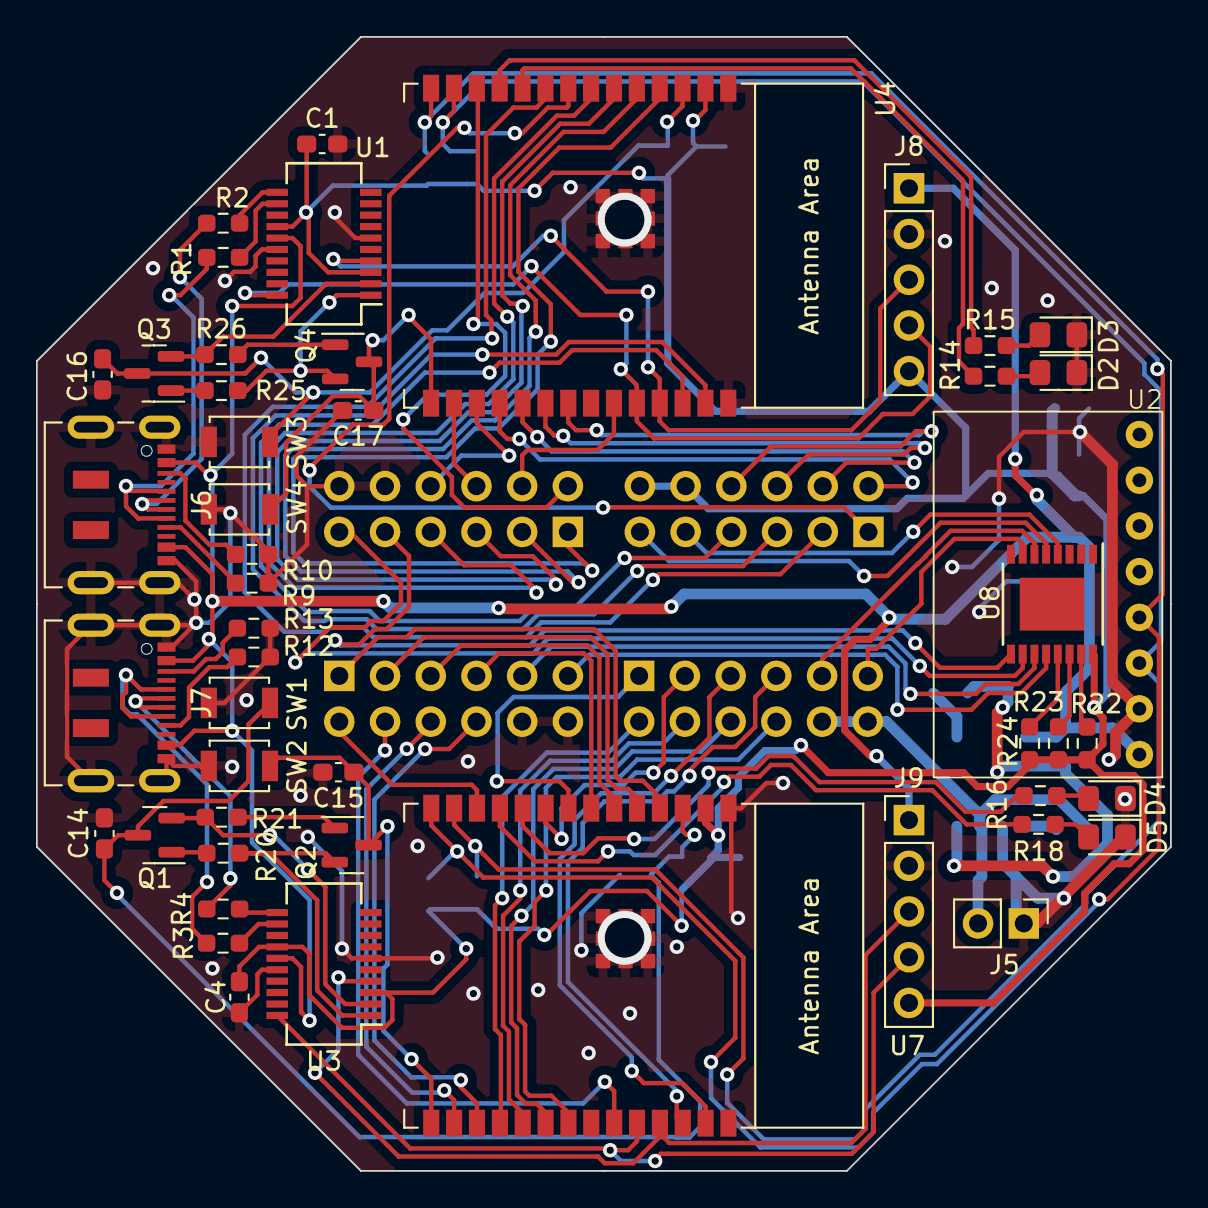
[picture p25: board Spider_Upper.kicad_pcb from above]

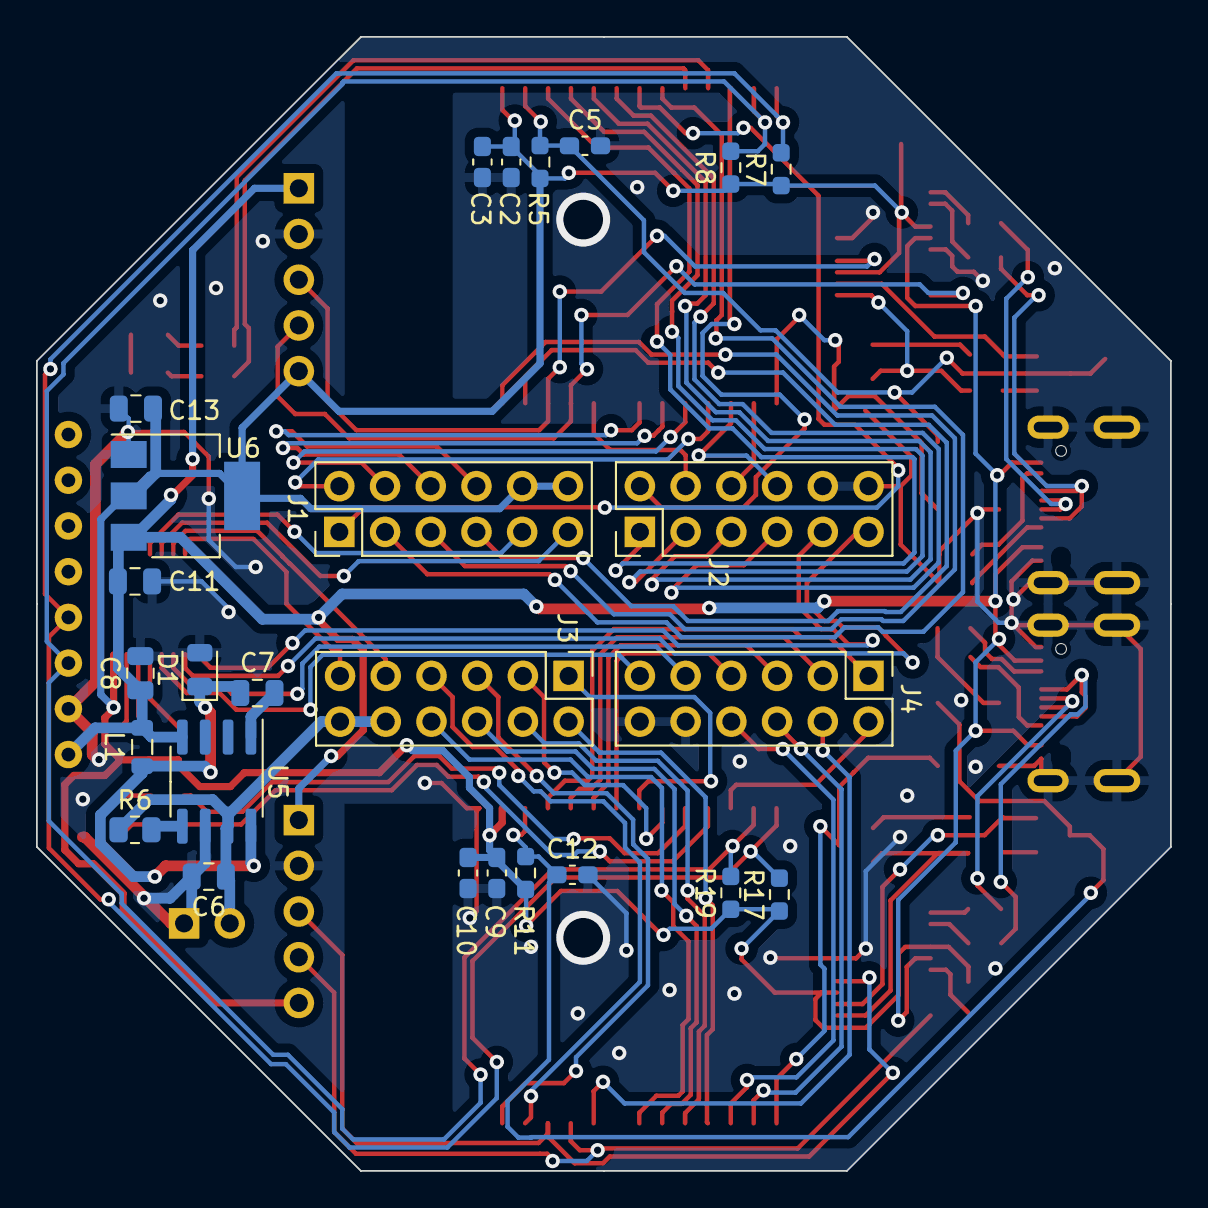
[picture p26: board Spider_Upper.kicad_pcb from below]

Board: 2 copper layers, 63.0 x 63.0 mm, 74 parts (26 on the bottom side), 88 nets.

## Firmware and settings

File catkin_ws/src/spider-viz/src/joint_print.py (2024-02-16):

#!/usr/bin/env python
import serial 
import rospy
import numpy as np
import time

from moveit_msgs.srv import GetPositionIK, GetPositionIKRequest, GetPositionIKResponse
from sensor_msgs.msg import JointState
from moveit_msgs.msg import RobotTrajectory
from trajectory_msgs.msg import JointTrajectoryPoint
from sensor_msgs.msg import JointState
from geometry_msgs.msg import Pose, PoseArray, WrenchStamped
from moveit_commander import MoveGroupCommander
from std_msgs.msg import Float32MultiArray

pub = None

def publisher():
    global pub
    pub = rospy.Publisher('joint_states', JointState, queue_size=10)
    r = rospy.Rate(10)
    
    while not rospy.is_shutdown():
        # Read Data
        if ESP_port.isOpen():
            read_val = str(ESP_port.readline().decode('utf-8'))
            joint_angles = parse_input(read_val)
            
            print(joint_angles)
            conv_angles = convert_states(joint_angles)
            push_states(conv_angles)

def convert_states(joint_angles):
    conv_angles = np.array(joint_angles)
    
    conv_angles = conv_angles - np.array([0.17, 1.1, 0.17, 1.1, 0.17, 1.1, 0.17, 1.1])
    conv_angles = conv_angles * np.array([-1, 1, 1, 1, 1, 1, -1, 1])
    
    
    
    return conv_angles

def push_states(angles):
    js = JointState()
    js.header.stamp = rospy.Time.now()
    js.name = ["Upper0", "Lower0", "Upper1", "Lower1", "Upper2", "Lower2", "Upper3", "Lower3"]
    js.position = angles
    pub.publish(js)


def parse_input(read_val):
    if read_val != "":
        try:
            angles = [float(i) * (np.pi/180) for i in read_val.split(" ")]
            return angles
        except:
            print("failed split")
    return []
    
    

if __name__ == '__main__':
    rospy.init_node('ESP_Interface') 
    
    ESP_port = serial.Serial(port='/dev/ttyUSB0', baudrate=115200, timeout=1)

    try:
        publisher()
    except rospy.ROSInterruptException: pass
    

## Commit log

2023-09-23 initial commit stuff
    [12V_Motor.SLDPRT, MF63zz 3x6x2.5mm Flanged Bearing.step.SLDPRT, SLS_Lever_upper.SLDPRT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]
2023-09-25 added homing switches
    [Homing Switch.SLDPRT, Limit_Switch.SLDPRT, Limit_Switch.STEP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]
2023-09-25 applied updates
    [SLS_body.SLDPRT, SLS_leg_upper.SLDPRT, SLS_leg_upper_M.SLDPRT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]
2023-09-25 created stl/moved sld files
    [12V_Motor.SLDPRT, Limit_Switch.SLDPRT, MF63zz 3x6x2.5mm Flanged Bearing.step.SLDPRT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]
2023-09-25 addedc colours
    [SLS_Lever_upper.SLDPRT, SLS_body.SLDPRT, SLS_leg_lower.SLDPRT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]
2023-10-02 modified stuff
    [SLS_Lever_upper.SLDPRT, SLS_Lever_upper.STL, SLS_body.SLDPRT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]
2023-10-02 updated body with more holes
    [SLS_body.SLDPRT, SLS_body.STL, SLS_lower_body.SLDPRT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]
2023-10-06 tried to export to urdf
    [12V_Motor.SLDPRT, Leg_lower_1.STL, Leg_lower_2.STL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]
2023-10-07 new URDF files
    [Leg_lower_1.STL, Leg_lower_2.STL, Leg_lower_3.STL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]
2023-10-09 updated urdf name
    [Leg_lower_1.STL, Leg_lower_2.STL, Leg_lower_3.STL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]
2023-10-14 updated URDF
    [Leg_lower_1.STL, Leg_lower_2.STL, Leg_lower_3.STL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]
2023-10-14 updated meshes
    [Leg_lower_1.STL, Leg_lower_2.STL, Leg_lower_3.STL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]
2023-10-14 testing part instead of asm
    [Leg_lower_1.STL, Leg_lower_2.STL, Leg_lower_3.STL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]
2023-10-14 updated URDF files again, hopefully for the last time
    [spider-viz.SLDASM, spider-viz.csv, spider-viz.urdf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]
2023-10-14 testing limits
    [lower_11.STL, lower_21.STL, lower_32.STL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]
2023-10-14 manually updated URDF file for simplified sollision
    [spider-viz.SLDASM, spider-viz.urdf]
2023-10-28 added testbenches
    [12V_Motor.SLDPRT, Let_TB_slider.SLDPRT, Limit_Switch.SLDPRT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]
2023-11-06 some prep to export to onshape
    [12V_Motor.SLDPRT, 12V_Motor.STEP, Limit_Switch.SLDPRT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]
2023-11-06 added heatset holes
    [Let_TB_slider.SLDPRT, SLS_body.SLDPRT, SLS_lower_body.SLDPRT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]
2023-12-11 progress on PCBs
    [Spider_Lower.kicad_pcb, Spider_Lower.kicad_sch, Spider_Lower.step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]
2023-12-13 finished V1 PCB
    [Spider_Upper.kicad_pcb, Spider_Upper.kicad_sch]
2023-12-16 pushing PCBs with STEP files
    [SLS_lever_lower.SLDPRT, Spider_Lower.kicad_pcb, Spider_Lower.kicad_sch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]
2024-01-02 i2c makes me want to kill myself
2024-01-05 added PID and cleaned up code
2024-01-08 added images
    [PCB_Lower.SLDPRT, PCB_Upper.SLDPRT, SLS_body.SLDPRT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]
2024-01-10 added battery holder
    [12V_Motor.SLDPRT, 12V_Motor.STEP, 6mm_magnet.SLDPRT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]
2024-01-10 exported new URDF file
    [12V_Motor.SLDPRT, 12V_Motor.STEP, Limit_Switch.SLDPRT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]
2024-01-10 ordf with joint limits
    [Lower0_Link.STL, Lower1_Link.STL, Lower2_Link.STL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]
2024-01-10 updated ros to do joint visualizer
